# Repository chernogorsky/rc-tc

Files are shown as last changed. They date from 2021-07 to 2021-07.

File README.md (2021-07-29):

# rc-tc
Railcore 300 Tool-Changer (HightTemp compatable)

STL is for files, original source was not publicly aviable

# Current status
Currently its a working setup, but has some minor flows to be addressed, so it may be named as a Beta stage.

I have fully functional 3 tool-heads (hemera, sherpamini+nova, bmg+mosquito, with space for another big tool), high-temp compatable (not all the plastic has been reprinted with HT version) tool changer based on RC300

# Goals

# E3D toolchange compatable railcore mod
Main goal of the project is to receive fully functiona tool changer printer based on RC300 supporint 4+ heads:
* e3d toolplate compatable. It should be able to use with little/no modification standard e3d TC heads
* e3d parking hardware compatable. Due to design diff e3d parking models may not be used without full redesign.

# High temperature compatable
Another objective is to have an option to perform under *135C* chamber temperature and HT extruders, 
So:
* all the motors are HT, or moved away from the chamber
* Z probe may be HT probe or HT microswitch
* all the plastic/other parts within enclosed area should be HT ready (HT plastic, silicon wiring, CNCed, ...)

# Stay as close to the original RC as possible
Here I want to be able to:
* utilize some of the upgrade I already have. so far in use:
  * all the frame alums upgrades
  * MR belts retainer
  * upper part of BMG ultralight mount (as part for BMG/Mosquito head)
* Be able to go back/forth without huge modification (currently its only removing the shaft)
 * you may use any plate-on mods, like mounts (except for fan shrounds)
 * no heavy hull mods 

# Dimentions
rc-tc-drawing

## Height Diff
Height diff between rail mounts and center of the shaft is "-6.6 mm"

## Z
Z is below the shaft center by 27.57 mm

## X
X is 35.85 mm and 41.45 mm both sides from the center of the shaft

## Y
Y is 29.85 mm (without bltouch/httouch) / 46.4 mm with from the back of the front plate (rail troley front side)

# BOM

## CNC
* Face plate should be CNCed
* May wont to mill/cnc twist lock

## Plastic part
* Since it's a HT version of the tool changer, all of the parts should be print with HT plastics, eventially
* No heavy force is expected to any of the parts, except for the back pulley, so it may be print by any HT plastic. 
* Back pulley is better to be print from something rigid and solid (Polymaker PCMAX; PC; etc) (for me  HT PLA with 100% infil works during all the tests)
* Parking mounts - have to be rigid matereal, probably with CF inside.

## Remote lock
You need all the details for remote lock from jubilee design

(Not a full list)
* motor (im using stepperonline, so my mount is for it) (stepperonline/filastruder) (mine is 14HS13-0804S-PG5)
* spring guide (https://www.filastruder.com/collections/jubilee/products/wire-cable-and-spring-guide-set-for-jubilee)
* alum hub (https://www.filastruder.com/collections/jubilee/products/aluminum-hub-6mm-id)
* pulley spring (2x https://www.filastruder.com/collections/jubilee/products/rel-replacement-extension-spring)
* twist lock (https://www.filastruder.com/collections/jubilee/products/twist-lock-assembly-for-jubilee) * should be cutted with dremmel

## Nozzle cleaning/whiping
Im using mod from e3d mod and bigbrain3d whiper. If you decide to do that, you'll need 
* HT pancake motor (LDO-42STH25-1404MAH)
* 35 mm round HT motor with 8/10 teaths gear installed (LDO-36STH17-1004AHG8 or LDO-36STH17-1004AHG Stepper)

## Tools
Im using e3d plate and docks, so you may need some of these:
* plate only 
* plate with dock (https://www.filastruder.com/products/e3d-toolchanger-blank-tool-plate-and-dock-kit?_pos=4&_sid=0a385e1ae&_ss=r)
* dock only (https://www.filastruder.com/products/e3d-toolchanger-dock-fixings-kit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)

## Electronics
This project is required you have control board with  support for:
* 5 axis (X, Y +3Z) steppers
* 4 (your number) heads steppers
* 1 remote lock motor steppers
* (optional) 1 remote probe servo control
* (optional) 2 steppers for HT wiper

My setup is duet3 6hc + 2x 3hc + 1x ToolBoard

## Power and electronics layouts
* I moved all the power supplies away from the printer
* I have 24V 400W rated (AWG12/16) main power lines
* I've utilized fully right side of the rc300 std electronic space and start using left side

## Enclosure/chamber
TBD,
there is a working solution from HighTemp3d, and several custom made

# Tested setups
## Original
Im using RC300 with: 
* alum full body (713Maker)
* all the alums upgrades (mandala rose + 713maker):
 * belt tention is from mandala rose
* magnum pulley (mandala rose)
* Halo for nema17 (713Maker)
* belts rated for 135C (e3d-online.com/hightemp3d.com)

* Enclosure TBD (mandala rose/hightemp3d/selfmade)

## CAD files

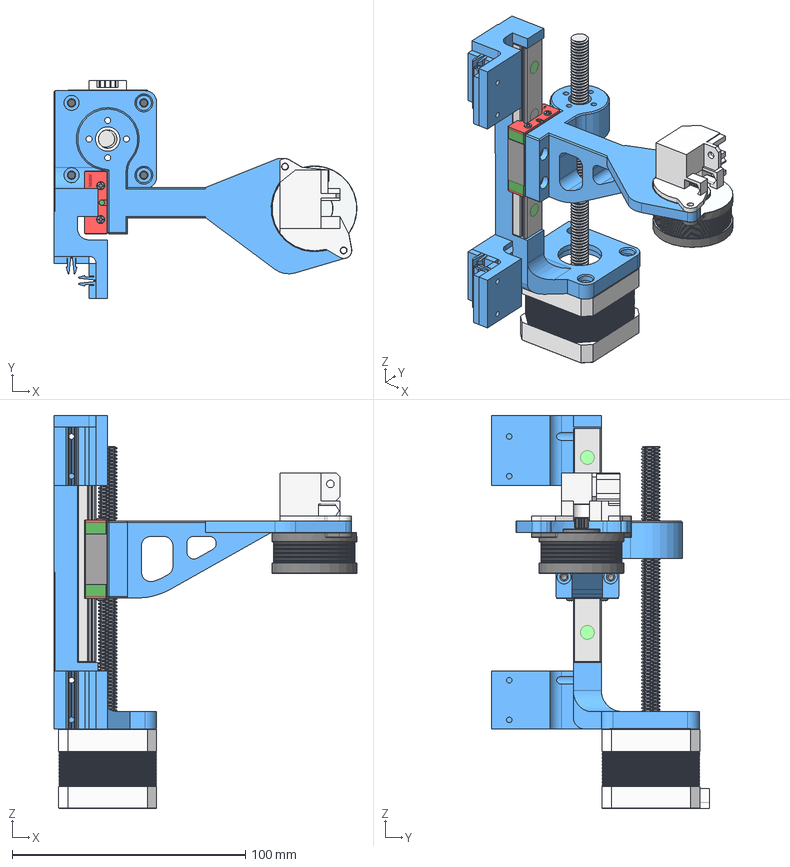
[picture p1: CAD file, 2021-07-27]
rc-tc-wiper.step
129.9 x 93.3 x 168.5 mm
rc_brush_rail x 4
MGNR12R110HM_FILE_1 v1 v3
NEMA 17 100mm Intergrated Leadscrew v2 v1
Brush_Arm_v2 v1
RC-TC-Purge-Body
NEMA14_10t^sherpa_mini_a3_r9c

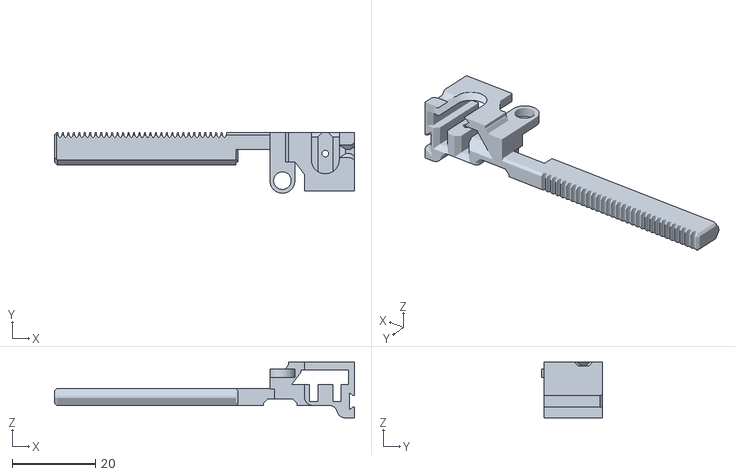
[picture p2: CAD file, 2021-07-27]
RC-TC-Wiper-Catcher.stl
72.0 x 14.5 x 13.4
